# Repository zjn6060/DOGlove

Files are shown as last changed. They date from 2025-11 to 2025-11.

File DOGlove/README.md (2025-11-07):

#A new fork from Jianai Zhao

# <a href="https://do-glove.github.io/">DOGlove: Dexterous Manipulation with a Low-Cost Open-Source Haptic Force Feedback Glove</a>

**Robotics: Science and Systems (RSS) 2025**

<a href="https://do-glove.github.io/"><strong>Project Page</strong></a> | 
<a href="https://arxiv.org/pdf/2502.07730"><strong>Paper</strong></a> | 
<a href="https://tea-lab.github.io/DOGlove/"><strong>Documentation</strong></a> | 
<a href="https://www.bilibili.com/video/BV19SLizUEfa/"><strong>30min工作讲解</strong></a>

[Han Zhang](https://doublehan07.github.io/)<sup>1,2</sup>,
[Songbo Hu](https://hsb0508.github.io/)<sup>1</sup>,
[Zhecheng Yuan](https://gemcollector.github.io/)<sup>1,2,3</sup>
[Huazhe Xu](http://hxu.rocks/)<sup>1,2,3</sup>

<sup>1</sup>Tsinghua University,
<sup>2</sup>Shanghai Qi Zhi Institute,
<sup>3</sup>Shanghai AI Lab

<div align="center">
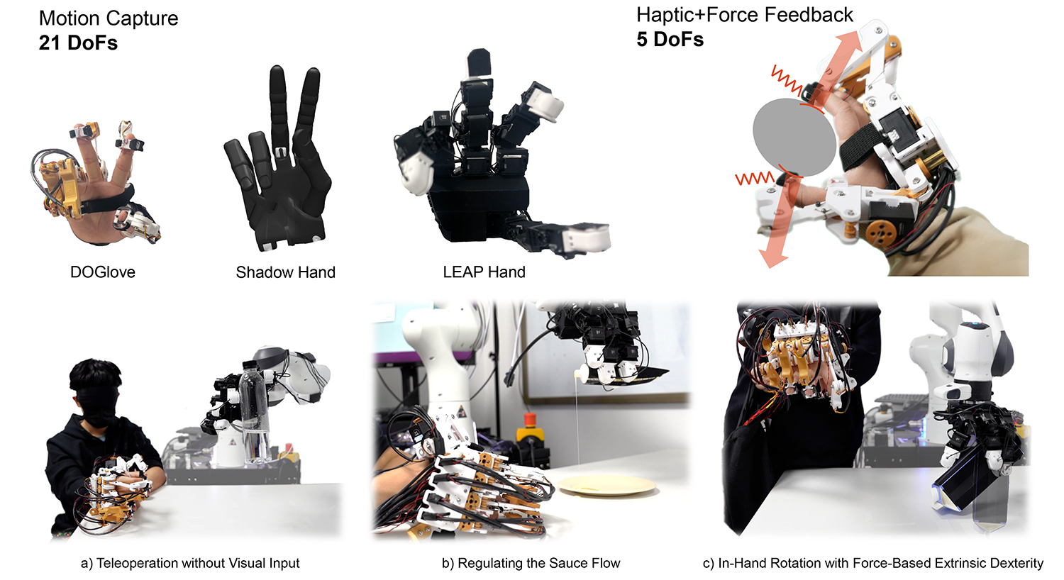
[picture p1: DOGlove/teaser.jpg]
teaser
  
</div>

## 🐣 Updates
* **2025/04/28** — Initial commit.
* **2025/05/11** — Added embedded firmware repository.
* **2025/06/01** — Added MakerWorld link, PCBA files, and Onshape model link.
* **2025/06/22** — Update the tutorial. Add the Python scripts.

## 🛠️ Environment Setup
**Tested on:** Ubuntu 20.04 LTS

### 1. Create Conda Environment
```bash
conda create -n DOGlove python=3.9.19
```

### 2. Install MuJoCo
```bash
conda install -c conda-forge mujoco
```

### 3. Install Required Python Packages
```bash
pip install -r requirements.txt
```

### 4. Install Dynamixel Wizard
Follow the [official installation guide](https://emanual.robotis.com/docs/en/software/dynamixel/dynamixel_wizard2/#install-linux):

1. Download the installer:
   [Linux Download](http://www.robotis.com/service/download.php?no=1671)
2. Grant permission:
   ```bash
   sudo chmod 775 DynamixelWizard2Setup_x64
   ```
3. Run the installer:
   ```bash
   ./DynamixelWizard2Setup_x64
   ```
4. Follow the prompts to complete installation.
5. Add your user to the `dialout` group to access the USB port:
   ```bash
   sudo usermod -aG dialout <your_account_id>
   # You can find your ID using:
   whoami
   ```
6. Reboot to apply the changes:
   ```bash
   sudo reboot
   ```

## 🧪 Run Test Scripts
```bash
conda activate DOGlove
python servo.py
python glove_mcu.py
python DOGlove_FK.py
```

## 🏷️ License
This repository is released under the MIT license. See [LICENSE](LICENSE) for more details.

## 👍 Acknowledgement
- Our wrist tracking code is adapted from [HTC Vive Tracker Python API](https://github.com/tianshengs/SteamVR_Tracking).
- Our Franka control code is adapted from [UMI](https://github.com/real-stanford/universal_manipulation_interface) and [Data Scaling Laws](https://github.com/Fanqi-Lin/Data-Scaling-Laws).
- Our 3D diffusion policy implementation is adapted from [3D Diffusion Policy](https://github.com/YanjieZe/3D-Diffusion-Policy) and [DemoGen](https://github.com/TEA-Lab/DemoGen).
- The teleoperation baseline (AnyTeleop) is implemented from [Dex Retargeting](https://github.com/dexsuite/dex-retargeting).

Contact [Han Zhang](https://doublehan07.github.io/) if you have any questions or suggestions.

## 📝 Citation
If you find our work useful, please consider citing:
```console
@article{zhang2025doglove,
  title={DOGlove: Dexterous Manipulation with a Low-Cost Open-Source Haptic Force Feedback Glove},
  author={Zhang, Han and Hu, Songbo and Yuan, Zhecheng and Xu, Huazhe},
  journal={arXiv preprint arXiv:2502.07730},
  year={2025}
}
```

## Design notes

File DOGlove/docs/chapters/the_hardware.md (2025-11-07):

# Hardware

DOGlove’s hardware consists of two main components: the electronics for sensing and control, and the mechanical structure for physical interaction.

```{toctree}
:hidden:
:maxdepth: 1

../hardware/01_circuit.rst
../hardware/02_mechanical.md
```

## Circuit Design

Learn how we designed the electronics for DOGlove, including the schematic, PCB layout, and how to import or preview the project:

* [Circuit Design](../hardware/01_circuit.rst)

## Mechanical Design

Explore the mechanical structure of DOGlove through a full Onshape model, which can be exported in various formats:

* [Mechanical Design](../hardware/02_mechanical.md)

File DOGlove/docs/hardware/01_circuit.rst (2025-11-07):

.. _circuit_design:

Circuit Design
==============

The Schematics
--------------

.. raw:: html

   <iframe src="../_static/hardware/SCH_DOGlove_MainCircuit.pdf" width="100%" height="600px"></iframe>

Import the Project File
------------------------

We use lceda (EasyEDA) to design the schematic and PCB layout. To preview the source project, you have two options:

Option 1: Import the `.epro` File
^^^^^^^^^^^^^^^^^^^^^^^^^^^^^^^^^

- **For users in China**: Use the `lceda Pro Edition (立创eda专业版) <https://pro.lceda.cn/editor>`__ to import the `.epro` file.
- **For users in other regions**: Use the `EasyEDA Pro Edition <https://pro.easyeda.com/editor>`__ to import the `.epro` file.

Steps to Import:

1. Download the :download:`ProPrj_DOGlove_MainBoard.epro <../_static/hardware/ProPrj_DOGlove_MainBoard.epro>` file.
2. Open EasyEDA Pro and navigate to ``File → Import → EasyEDA (Professional)``.

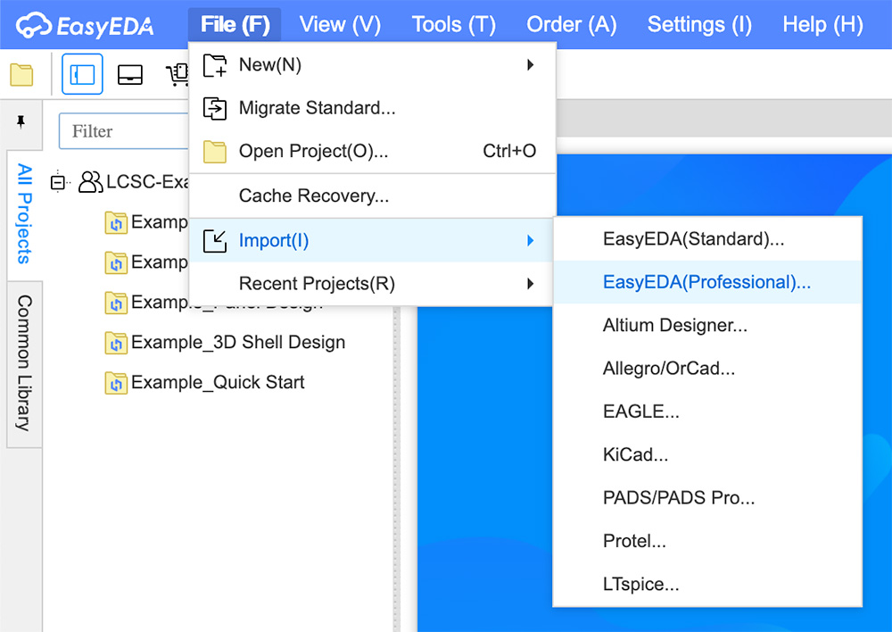
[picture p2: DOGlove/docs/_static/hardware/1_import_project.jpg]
   

3. Upload the `.epro` file, adjust the settings as shown below, then click **Import**:
   
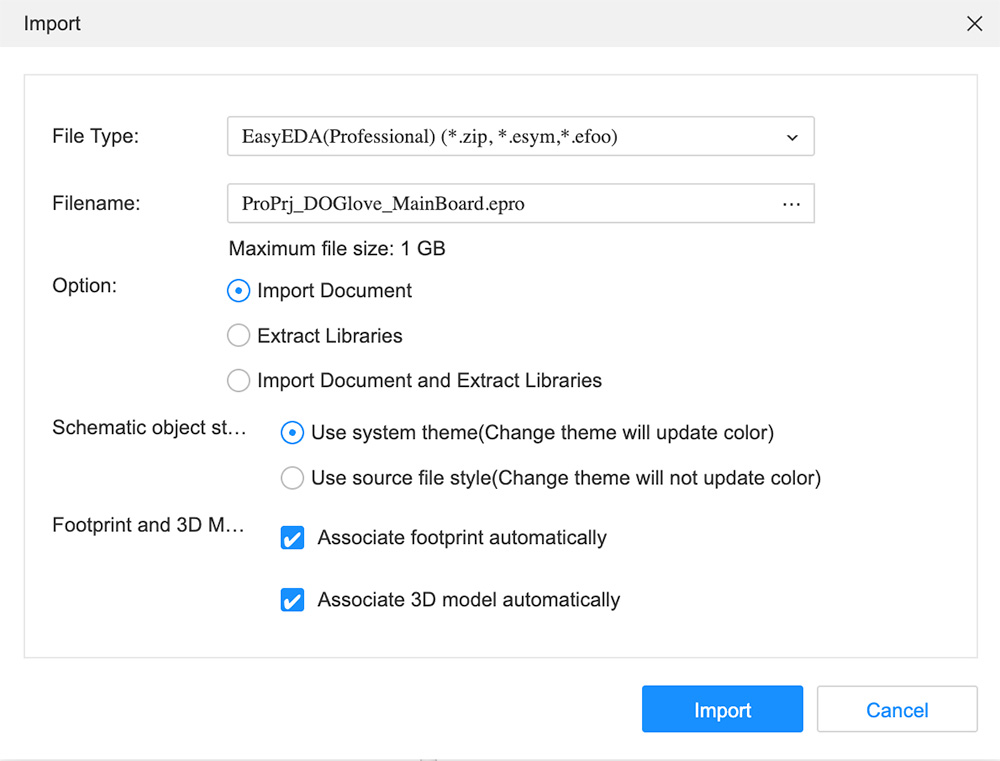
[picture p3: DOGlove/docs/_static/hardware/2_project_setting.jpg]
   

4. Confirm the import settings and click **Save**:

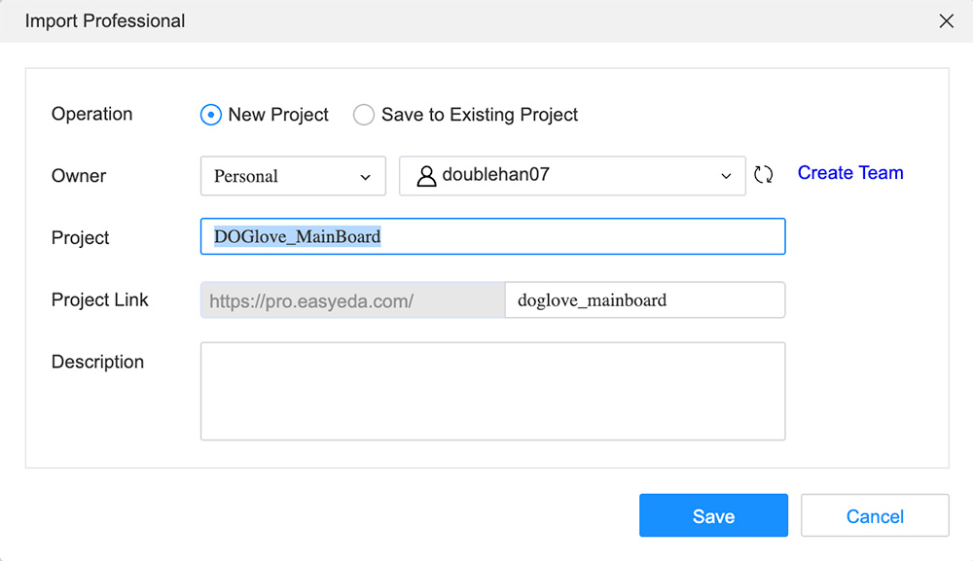
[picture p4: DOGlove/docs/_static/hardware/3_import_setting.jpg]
   

5. You should now see the full schematic and layout preview:

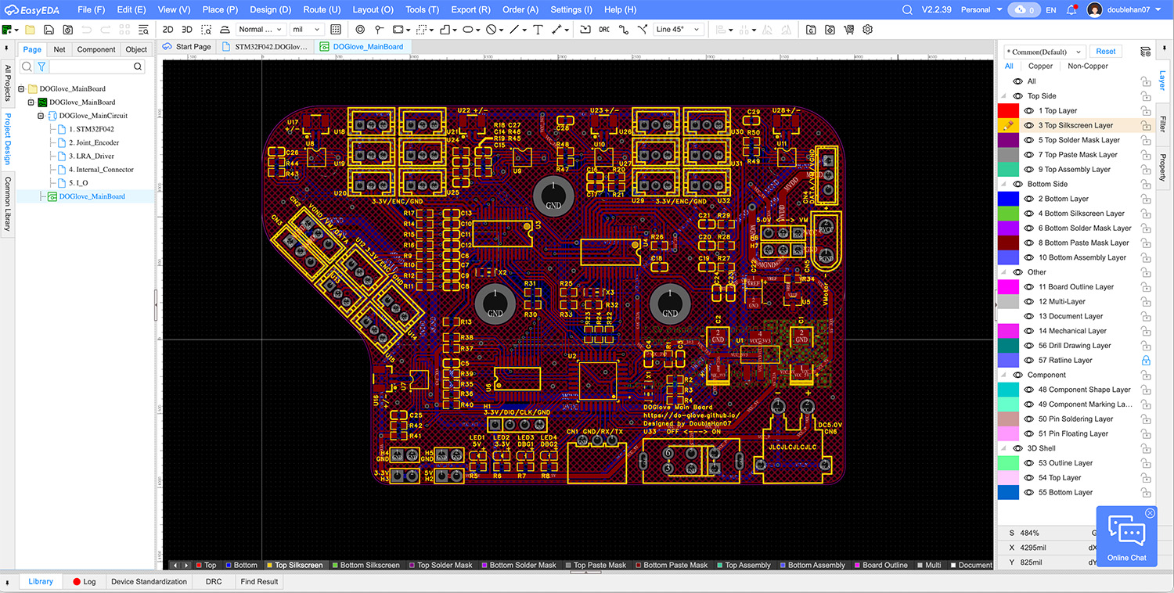
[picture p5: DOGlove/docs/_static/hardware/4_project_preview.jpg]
   

Option 2: View on OSHWHub (Recommended for Users in China)
^^^^^^^^^^^^^^^^^^^^^^^^^^^^^^^^^^^^^^^^^^^^^^^^^^^^^^^^^^^

You can directly view the `DOGlove project on OSHWHub (立创开源硬件平台) <https://oshwhub.com/doublehan/doglove_mainboard>`__, which includes the schematics, PCB layout, and BOM. The platform also supports one-click PCB fabrication.

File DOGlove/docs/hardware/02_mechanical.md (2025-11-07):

# Mechanical Design

You can view the 3D model of DOGlove on Onshape. The model can be exported to SolidWorks, STEP, IGES, STL, and other formats supported by Onshape.

[🧩 Onshape: 3D Model](https://cad.onshape.com/documents/7fa03943c40f265f7147311f)

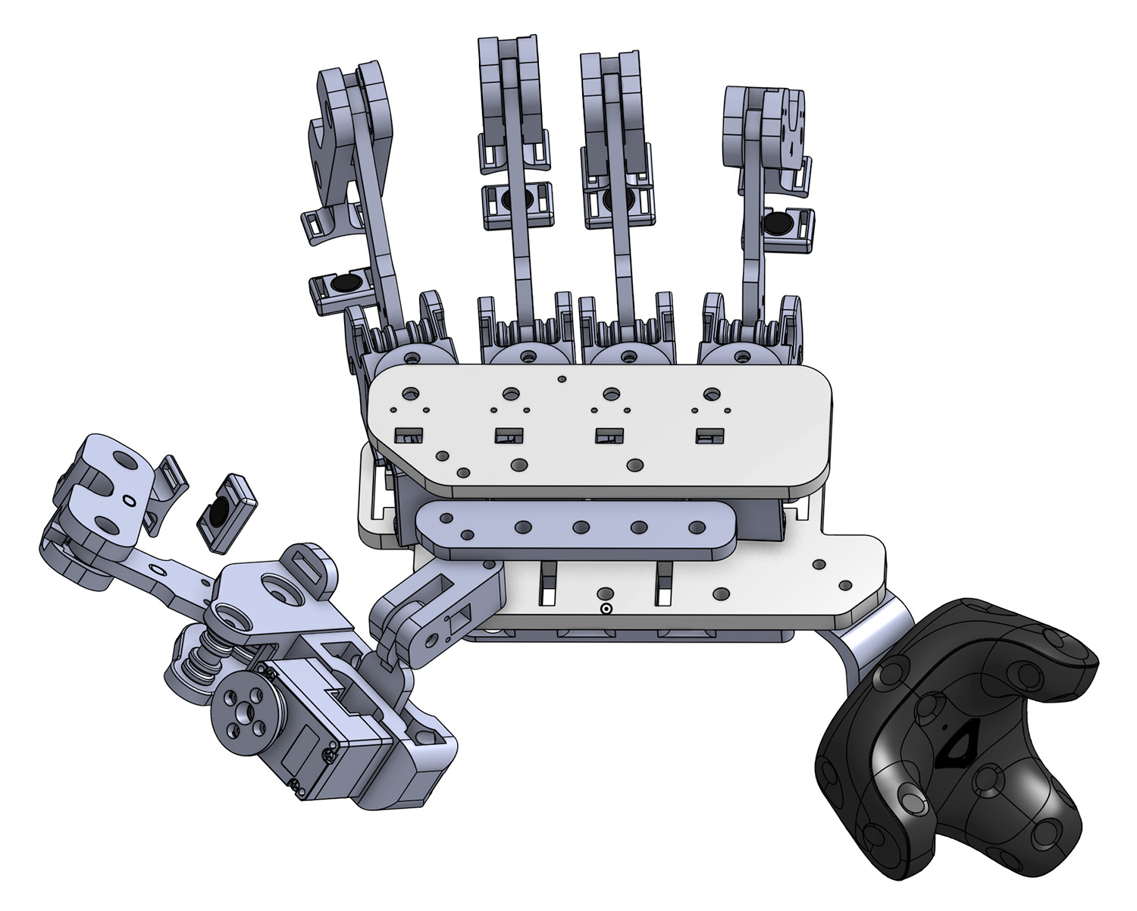
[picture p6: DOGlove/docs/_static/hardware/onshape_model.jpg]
Onshape Model Preview


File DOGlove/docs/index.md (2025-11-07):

# DOGlove

DOGlove is a low-cost, open-source haptic+force feedback glove designed for dexterous manipulation and teleoperation.  

Check out some useful links below to learn more:

[🌐 Website](https://do-glove.github.io/) | 
[📄 Paper](https://arxiv.org/pdf/2502.07730) | 
[🎥 Video](https://www.youtube.com/watch?v=2qO7dbH9zxc) | 
[𝕏 Tweet](https://x.com/DoubleHan07/status/1889815837810499688)

[🧩 Onshape: 3D Model](https://cad.onshape.com/documents/7fa03943c40f265f7147311f)

[🛠️ MakerWorld: Bambu 3mf Files](https://makerworld.com/en/models/1476400-doglove#profileId-1541008)

[📟 Circuit Board: OSHWHub (lceda)](https://oshwhub.com/doublehan/doglove_mainboard)

[⚙️ Firmware: STM32 Source Code](https://github.com/doublehan07/DOGlove_Firmware)

---

## Getting Started

Ready to dive in? We've prepared a [detailed tutorial](chapters/getting_started) to help you build your own DOGlove!

If you're new to DOGlove, the easiest way is to follow the step-by-step tutorial☝️.  
For experienced developers, we also highlight the key steps below👇:

- **Flash the embedded firmware**: Check out the [firmware](quick_start/03_flash_firmware) script.
- **Bring it to life**: Quick link to [make it move](quick_start/05_make_it_move).

## Customizing

Want to customize your DOGlove, explore the key design ideas, or contribute to the project?  
Check out the following sections for more details!

* [Hardware](chapters/the_hardware): Circuit design details and 3D printable models.
* [Firmware](chapters/the_firmware): Embedded firmware that runs on DOGlove.
* [Software](chapters/the_software): Python API and interface to control DOGlove.

## Troubleshooting

<!-- If you encounter any issues or have suggestions for improvements, feel free to [open a GitHub issue]()!   -->
If you encounter any issues or have suggestions for improvements, feel free to open a GitHub issue.   
We'd love to hear from you.

```{toctree}
:maxdepth: 1
:hidden:

chapters/getting_started
chapters/the_hardware
chapters/the_firmware
chapters/the_software

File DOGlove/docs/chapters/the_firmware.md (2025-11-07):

# Firmware

The source code of the firmware is listed [here](https://github.com/doublehan07/DOGlove_Firmware).

## Use the Firmware

You can download the precompiled firmware from the following link and flash it to the STM32:
[DOGlove.hex](https://github.com/doublehan07/DOGlove_Firmware/releases/download/v1.0/DOGlove.hex)

## Build from Source Code

To build the firmware from source:

```bash
git clone https://github.com/doublehan07/DOGlove_Firmware.git
cd DOGlove_Firmware
make
```

> 💡 Note: You may need to install [arm-none-eabi-gcc](https://developer.arm.com/downloads/-/gnu-rm) to compile the firmware.

## Notes for Advanced Developers

To modify the firmware or view pin configurations, open the [DOGlove.ioc](https://github.com/doublehan07/DOGlove_Firmware/blob/main/DOGlove.ioc) file using [STM32CubeMX](https://www.st.com/en/development-tools/stm32cubemx.html).

### Pin Allocation

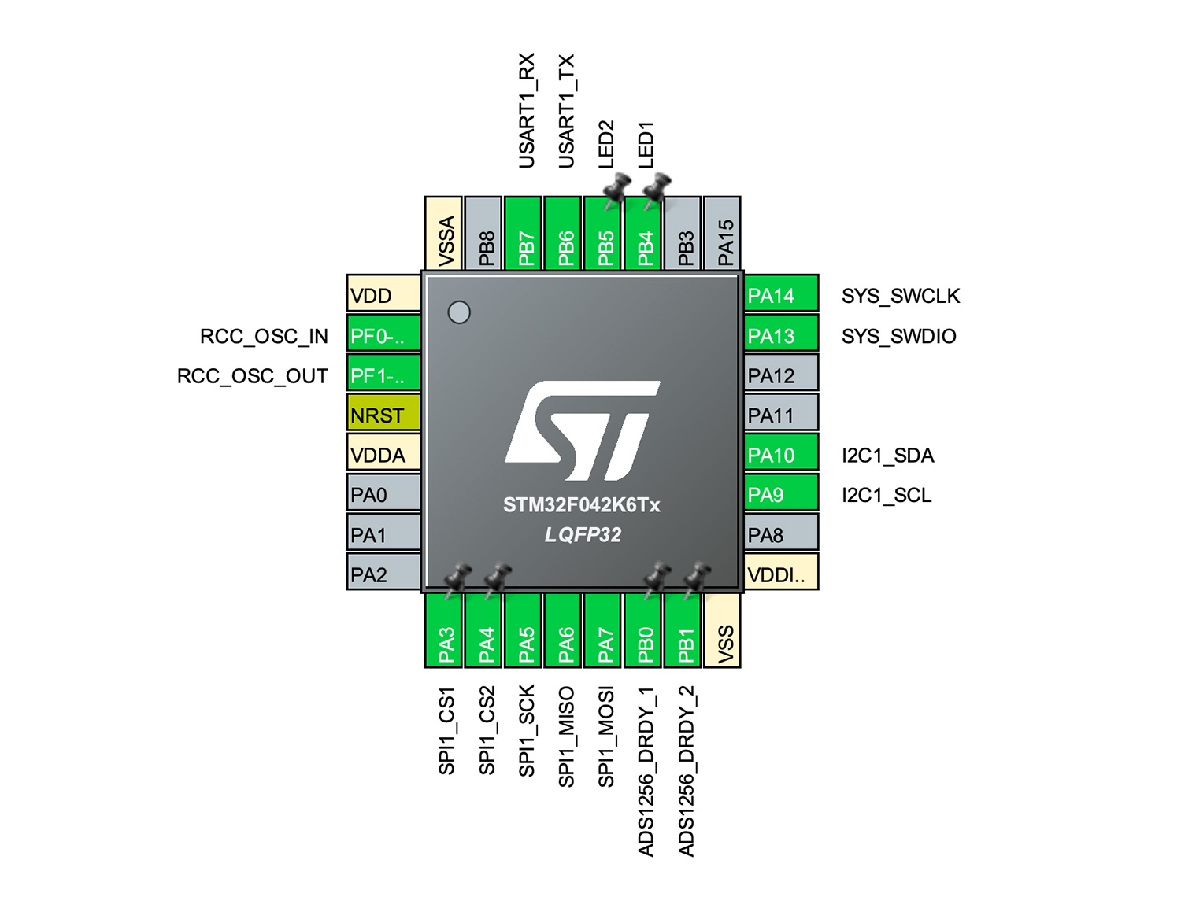
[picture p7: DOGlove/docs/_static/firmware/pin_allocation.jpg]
Pin Allocation


### Clock Tree Configuration

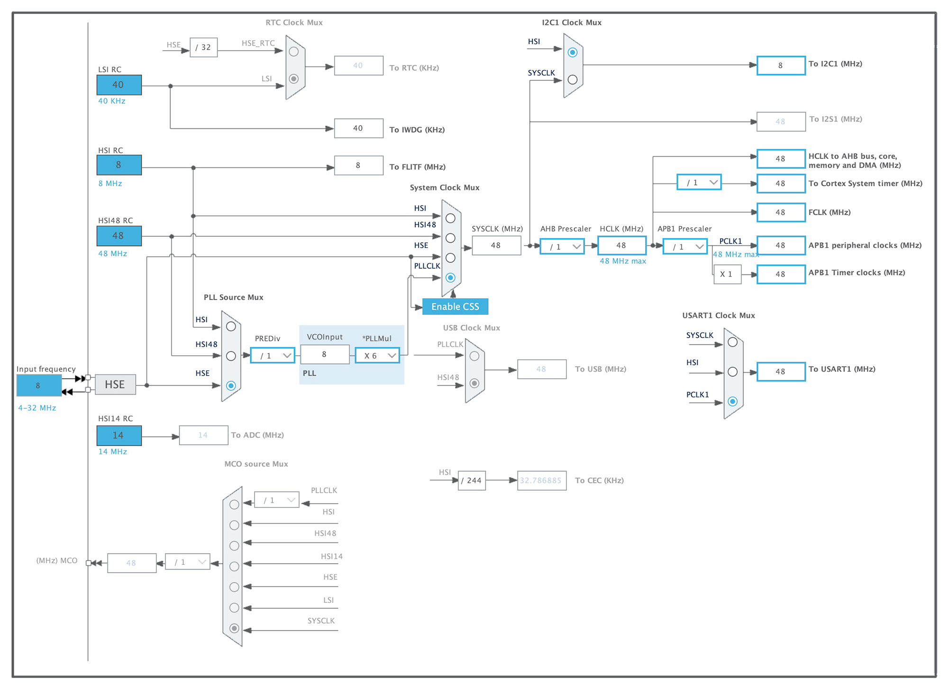
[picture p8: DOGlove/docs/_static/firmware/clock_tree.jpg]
Clock Tree


### Source Code Structure

* [/Core](https://github.com/doublehan07/DOGlove_Firmware/tree/main/Core): *(Auto-generated by STM32CubeMX, except for `main.c` and `stm32f0xx_it.c`)*

  * [main.c](https://github.com/doublehan07/DOGlove_Firmware/blob/main/Core/Src/main.c): System initialization, LRA control, and encoder data packaging.
  * [stm32f0xx\_it.c](https://github.com/doublehan07/DOGlove_Firmware/blob/main/Core/Src/stm32f0xx_it.c): SysTick handler used for system-level scheduling.

* [/Drivers](https://github.com/doublehan07/DOGlove_Firmware/tree/main/Drivers): STM32 HAL drivers *(auto-generated)*

* [/Users](https://github.com/doublehan07/DOGlove_Firmware/tree/main/Users): Custom drivers and application code.

  * [ads1256.c](https://github.com/doublehan07/DOGlove_Firmware/blob/main/Users/ads1256.c): ADC driver for the ADS1256 chip.
  * [drv2605l.c](https://github.com/doublehan07/DOGlove_Firmware/blob/main/Users/drv2605l.c): Haptic driver for the DRV2605L chip.
  * [tca9548a.c](https://github.com/doublehan07/DOGlove_Firmware/blob/main/Users/tca9548a.c): I2C multiplexer driver for the TCA9548A chip.
  * [fsr.c](https://github.com/doublehan07/DOGlove_Firmware/blob/main/Users/fsr.c): Reads power supply voltage via STM32's internal ADC.
  * [delay.c](https://github.com/doublehan07/DOGlove_Firmware/blob/main/Users/delay.c): Implements precise millisecond-level delay.
  * [lra\_control.c](https://github.com/doublehan07/DOGlove_Firmware/blob/main/Users/lra_control.c): LRA control logic and UART RX event callback.

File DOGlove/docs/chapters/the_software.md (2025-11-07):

# Software

This section outlines the key components of the software stack for DOGlove, including communication protocols, servo control, feedback mechanisms, and calibration.

## Communication Between PC and Main Board

- **UART Package** – Used for low-level serial communication.  
- **Vibration Package** – Responsible for encoding and transmitting vibration feedback.  
- **UDP** – Used for real-time data streaming between the glove and host computer.

## Servo Data Path

- **UDP** – Servo position commands and sensor data are transmitted over UDP for low-latency control.

## Haptic + Force Feedback

- **Force Sensor Readings** – Captures contact forces at the robot fingertips.
- **Force Feedback Activation Threshold** –  
  When the measured force exceeds a preset threshold, force feedback is enabled by turning on `servo.torque`.

  - To adjust the *stiffness* of the force feedback, modify the `Kp` gain parameter.

- **Vibration Activation Threshold** –  
  When a separate threshold is crossed, the MCU sends vibration commands to the glove.

  - You can adjust the **vibration pattern** and **duration** using the TI vibration library.

## Forward and Inverse Kinematics (FK & IK)

- Add the **site name** in the corresponding `.xml` file to support FK/IK calculations for the pinky finger.

## Calibration: Scale and Shift

To ensure realistic hand motion mapping, we apply scale and shift adjustments:

- **Finger Length Discrepancy → Scale Factor**  
  Scale the glove’s finger motion to match the relative lengths of the robotic hand.

- **Finger Distance Discrepancy → Shift Offset**  
  Adjust for base position differences between fingers to ensure accurate positioning.

The goal is simple: when the real thumb and index finger touch, the robot’s thumb and index should touch as well.

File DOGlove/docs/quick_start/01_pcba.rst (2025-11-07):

.. _tutorials_en:

=================
PCB Assembly
=================

- `Step-by-step Tutorial (English) <#tutorials_en>`_

Step-by-Step Guide to Ordering PCBA
====================================

This tutorial walks you through how to order the DOGlove main board through `JLCPCB <https://cart.jlcpcb.com/quote>`_.

.. note::
   You're free to choose any PCBA manufacturer you prefer. In general, you'll need to submit a **Gerber file** (for PCB fabrication) and **Pick & Place + BOM files** (for SMT assembly).

1. File Preparation
-------------------

- :download:`Download Gerber file <../_static/quick_start/pcba/Gerber_DOGlove_MainBoard.zip>`
- :download:`Download Pick & Place file <../_static/quick_start/pcba/PickAndPlace_DOGlove_MainBoard.xlsx>`
- :download:`Download BOM file <../_static/quick_start/pcba/BOM_DOGlove_MainBoard_DOGlove_MainBoard.xlsx>`

2. Order the PCB
------------------

**Step 1:** Upload the Gerber file you just downloaded.

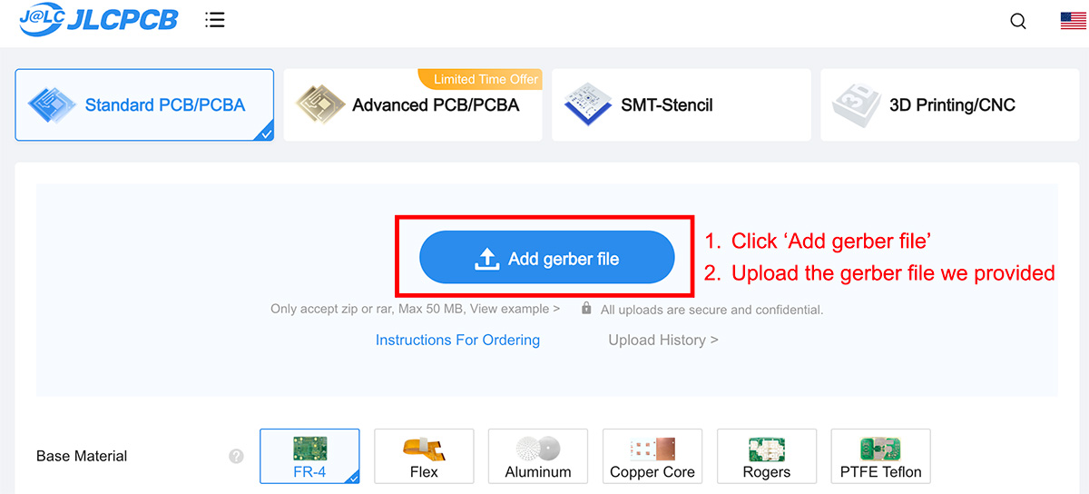
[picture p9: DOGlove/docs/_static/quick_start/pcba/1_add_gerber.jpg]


**Step 2:** Follow the image tutorial below to select the appropriate manufacturing parameters.

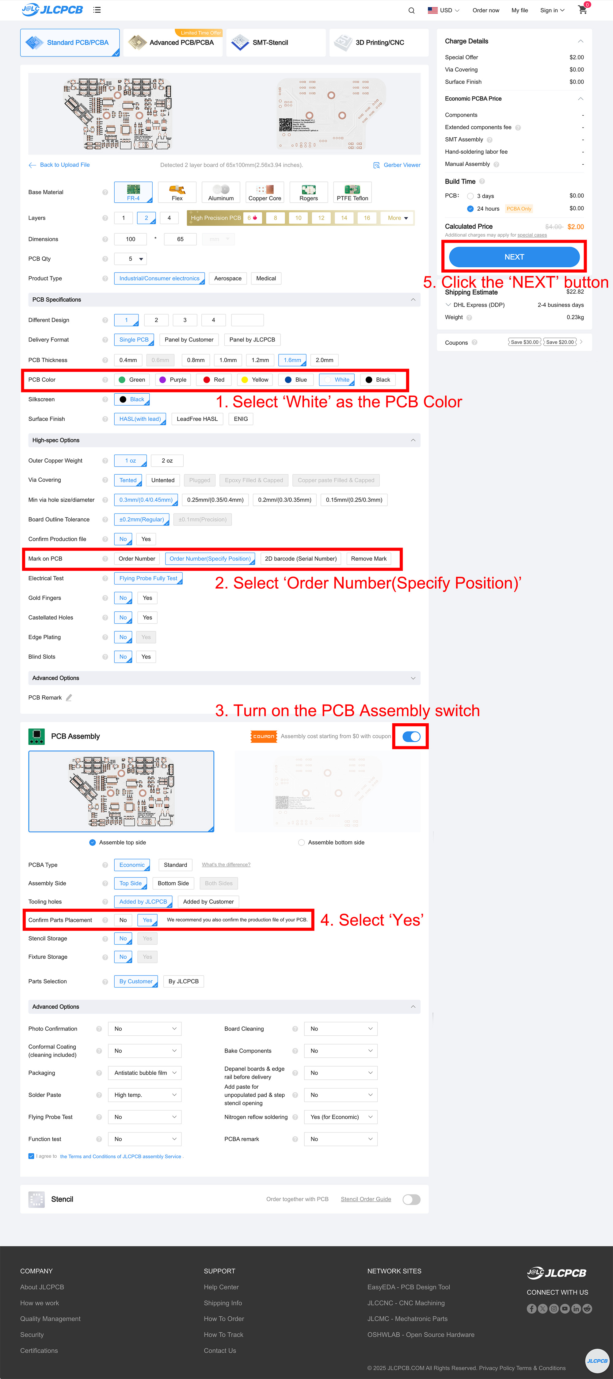
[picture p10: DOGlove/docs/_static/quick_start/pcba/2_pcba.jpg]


**Step 3:** On the next page, open the ``Bill of Materials`` section and upload both the **BOM** and **Pick & Place** files.

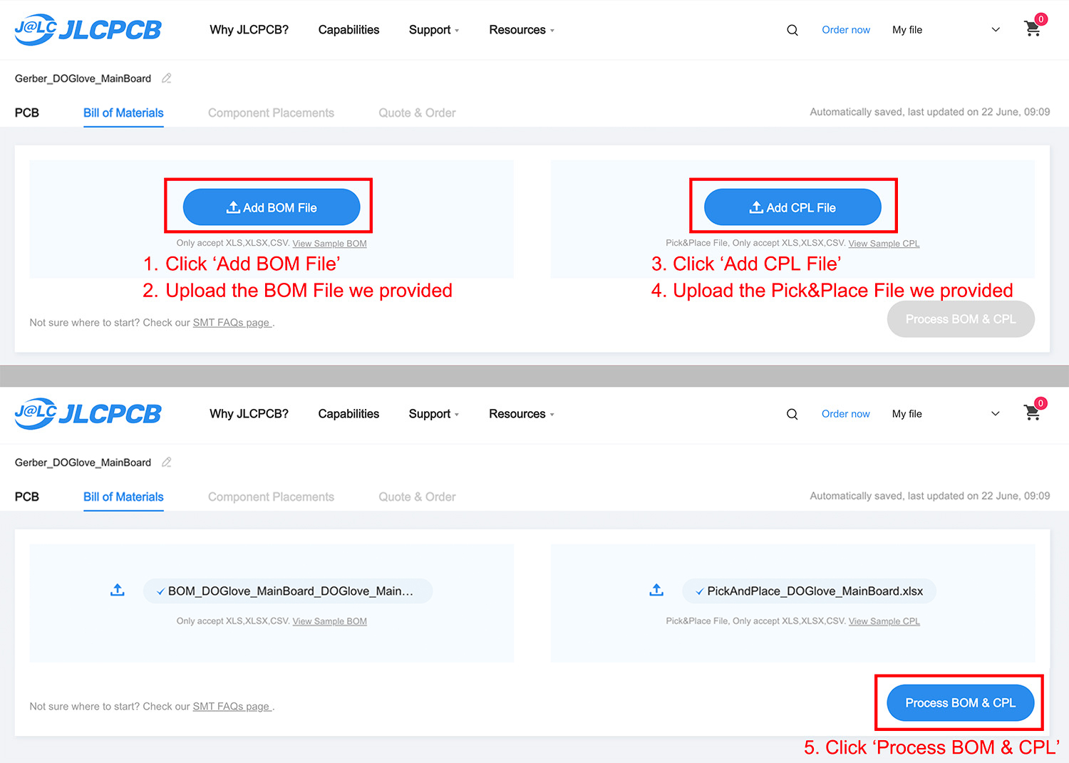
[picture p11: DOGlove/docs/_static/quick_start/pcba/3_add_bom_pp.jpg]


**Step 4:** Once processed, a parts confirmation list will be shown. If all parts are in stock, click **NEXT** to proceed.

.. tip::
   If some parts are unavailable, manually select substitutes using the suggestions provided. 

   Need help? Open a GitHub issue or contact Han directly.

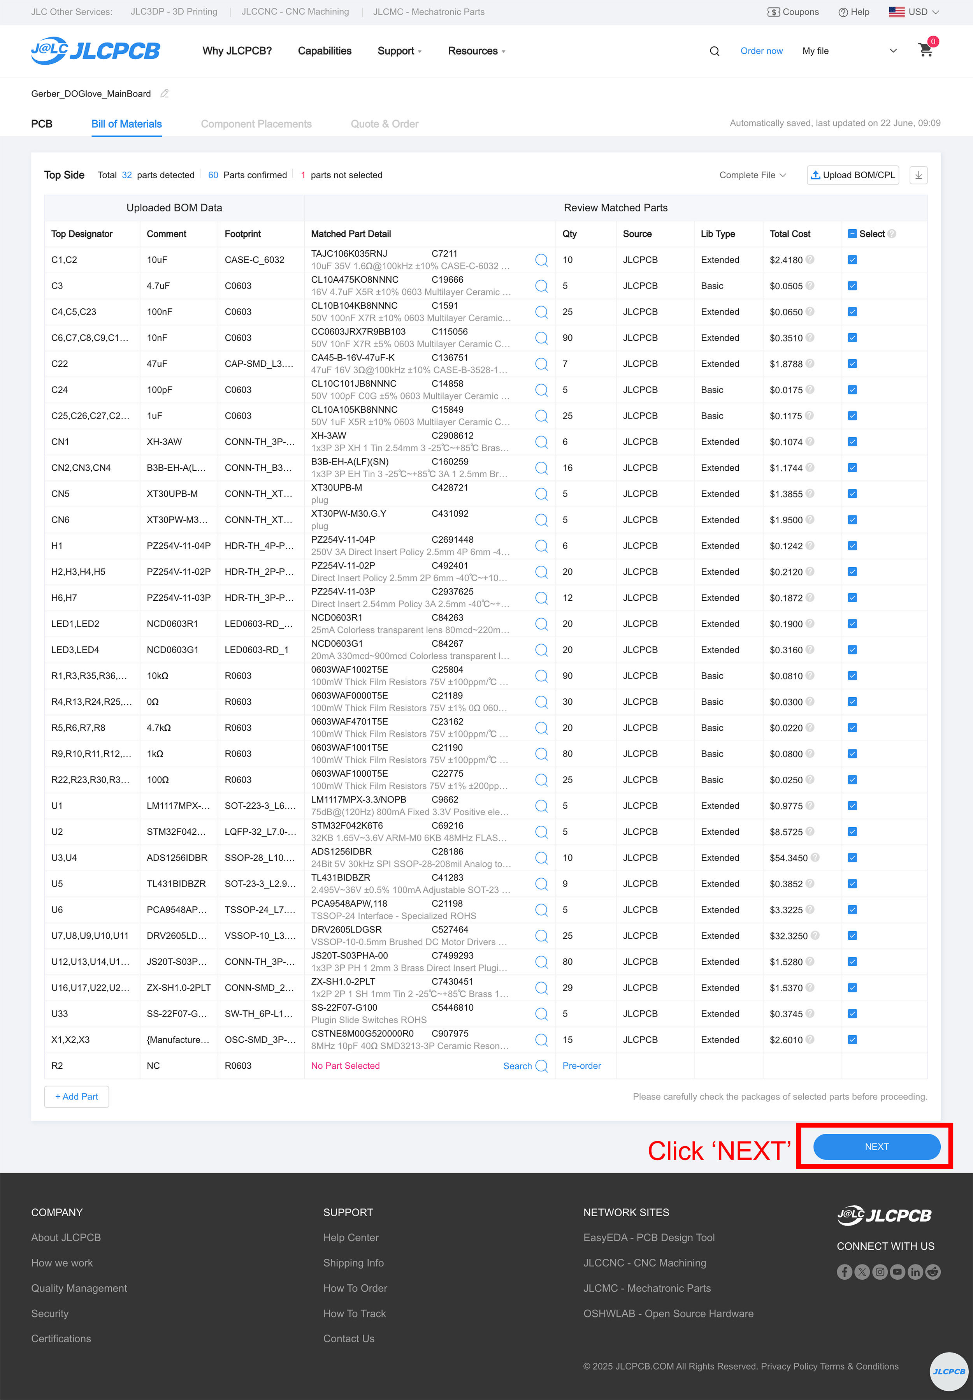
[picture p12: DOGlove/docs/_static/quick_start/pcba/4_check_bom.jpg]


**Step 5:** You might see a warning like *"Project has unselected parts."* This is normal, as some NC (Not Connected) parts are not meant to be assembled. Just click **Do not place** to continue.

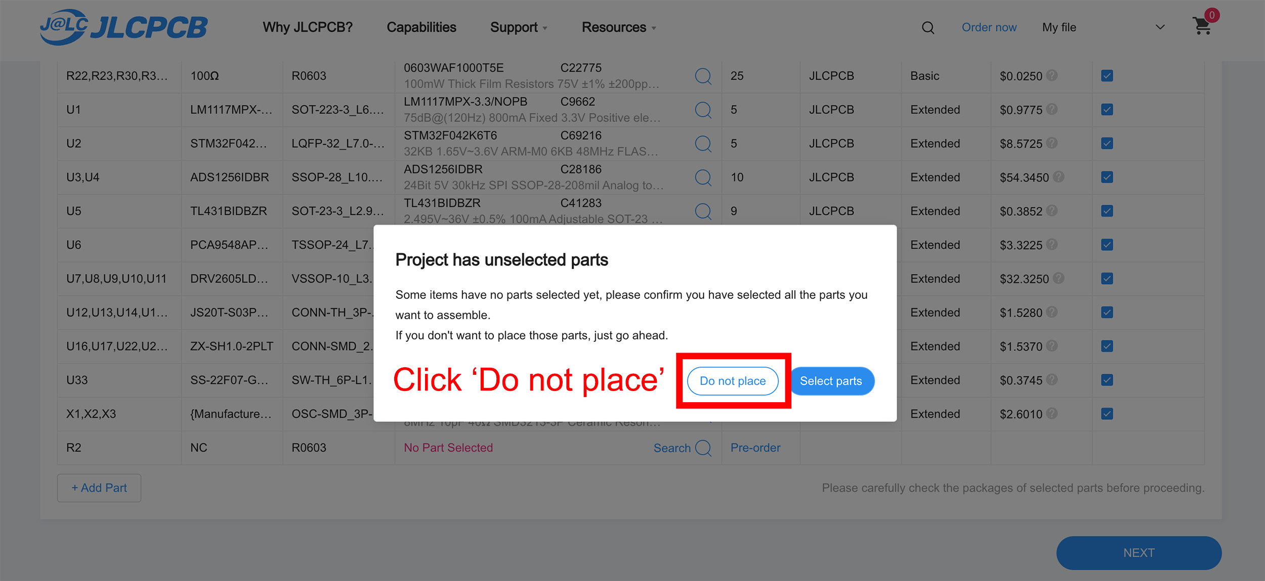
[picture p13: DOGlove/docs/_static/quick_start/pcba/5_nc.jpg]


**Final Step:** 🎉 You’re almost there! You can now preview a 3D model of your assembled board. If everything looks good and matches the preview images, click **NEXT** to place your order!

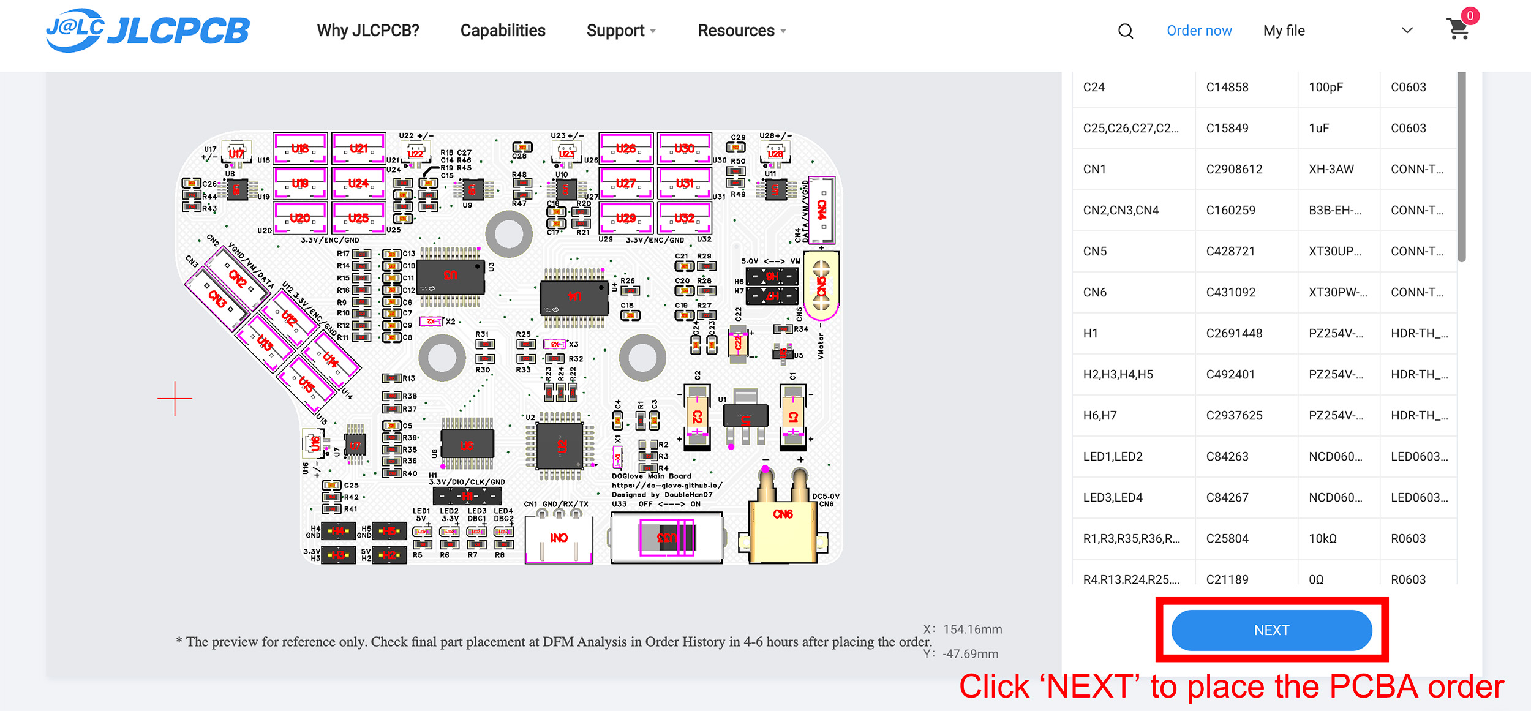
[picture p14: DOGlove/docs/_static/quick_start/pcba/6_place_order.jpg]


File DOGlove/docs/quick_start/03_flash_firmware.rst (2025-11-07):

.. _flash-firmware:

Flash the Firmware
==================

First, follow the image below to correctly connect the main board to the ST-Link V2.

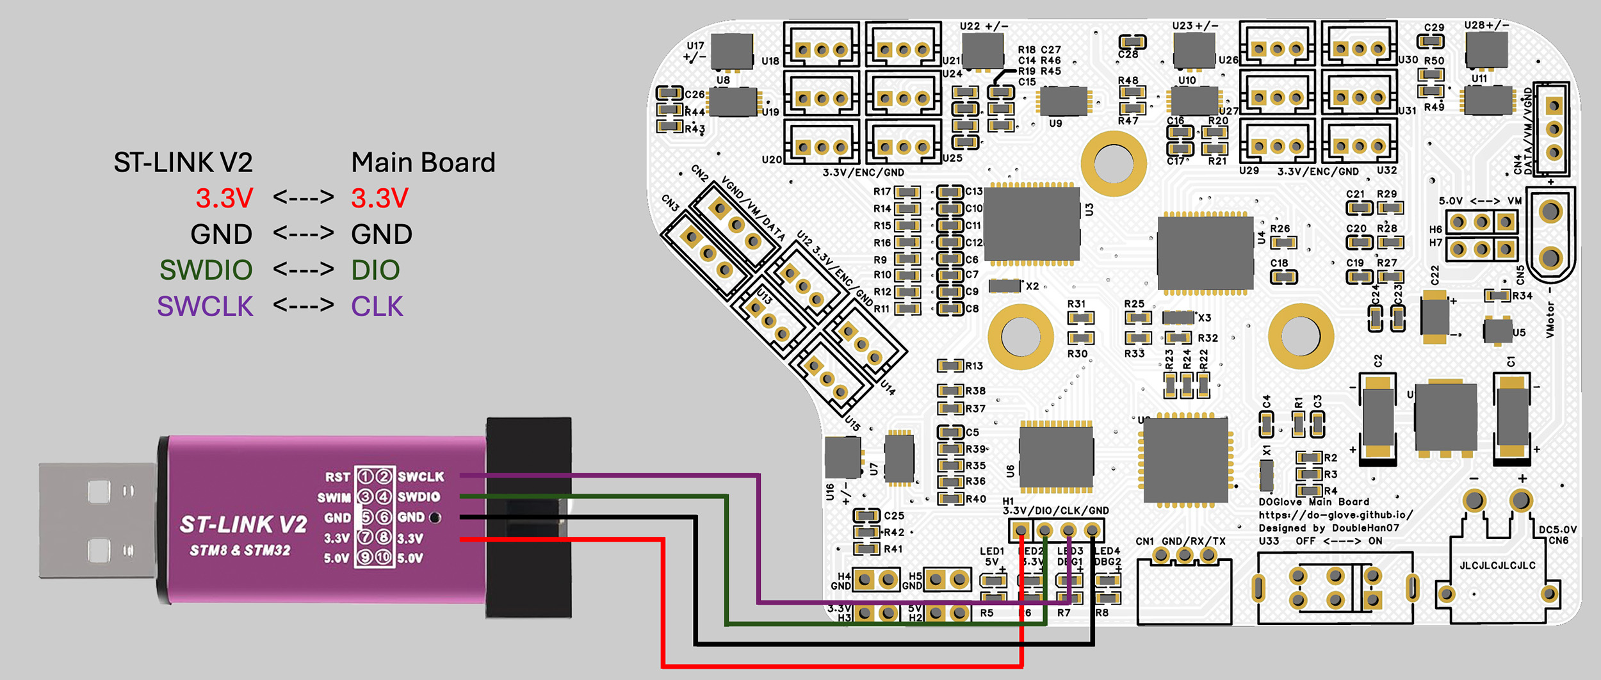
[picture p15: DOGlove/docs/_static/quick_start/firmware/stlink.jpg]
Connect main board to ST-Link V2


Next, download the latest firmware:

- :download:`DOGlove firmware <https://github.com/doublehan07/DOGlove_Firmware/releases/download/v1.0/DOGlove.hex>`

Then you need a tool to flash the firmware into the STM32 MCU (Microcontroller).

For Ubuntu, we suggest `openocd <https://openocd.org/pages/getting-openocd.html>`_.

.. note::

   Our whole system is verified under Ubuntu 20.04. 
   
   For macOS, you can also use `openocd` by running ``brew install open-ocd``. 
   
   For Windows, consider using the `STM32Programmer <https://www.st.com/en/development-tools/stm32cubeprog.html>`_.

To install openocd, simply type this command:

.. code-block:: bash

   sudo apt-get install openocd

Then change directory to the firmware location:

.. code-block:: bash

   cd <YOUR_FIRMWARE_LOCATION>
   openocd -f interface/stlink-v2.cfg -f target/stm32f0x.cfg -c "program DOGlove.hex verify reset exit"

If everything goes well, you might see the following message:

.. code-block:: text

   flash verify OK

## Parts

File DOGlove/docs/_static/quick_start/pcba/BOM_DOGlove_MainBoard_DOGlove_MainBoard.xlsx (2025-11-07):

No. | Quantity | Comment | Designator | Footprint | Value | Manufacturer Part | Manufacturer | Supplier Part | Supplier
1 | 2 | 10uF | C1,C2 | CASE-C_6032 | 10uF | TAJC106K035RNJ | Kyocera AVX | C7211 | LCSC
2 | 1 | 4.7uF | C3 | C0603 | 4.7uF | CL10A475KO8NNNC | SAMSUNG(三星) | C19666 | LCSC
3 | 3 | 100nF | C4,C5,C23 | C0603 | 100nF | CL10B104KB8NNNC | SAMSUNG(三星) | C1591 | LCSC
4 | 16 | 10nF | C6,C7,C8,C9,C10,C11,C12,C13,C14,C15,C16,C17,C18,C19,C20,C21 | C0603 | 10nF | CC0603JRX7R9BB103 | YAGEO(国巨) | C115056 | LCSC
5 | 1 | 47uF | C22 | CAP-SMD_L3.5-W2.8-R-RD | 47uF | CA45-B-16V-47uF-K | CEC(振华新云) | C136751 | LCSC
6 | 1 | 100pF | C24 | C0603 | 100pF | CL10C101JB8NNNC | SAMSUNG(三星) | C14858 | LCSC
7 | 5 | 1uF | C25,C26,C27,C28,C29 | C0603 | 1uF | CL10A105KB8NNNC | SAMSUNG(三星) | C15849 | LCSC
8 | 1 | XH-3AW | CN1 | CONN-TH_3P-P2.54_HCTL_XH-3AW |  | XH-3AW | HCTL(华灿天禄) | C2908612 | LCSC
9 | 3 | B3B-EH-A(LF)(SN) | CN2,CN3,CN4 | CONN-TH_B3B-EH-A-LF-SN |  | B3B-EH-A(LF)(SN) | JST | C160259 | LCSC
10 | 1 | XT30UPB-M | CN5 | CONN-TH_XT30UPB-M |  | XT30UPB-M | AMASS(艾迈斯) | C428721 | LCSC
11 | 1 | XT30PW-M30.G.Y | CN6 | CONN-TH_XT30PW-M |  | XT30PW-M30.G.Y | AMASS(艾迈斯) | C431092 | LCSC
12 | 1 | PZ254V-11-04P | H1 | HDR-TH_4P-P2.54-V-M |  | PZ254V-11-04P | XFCN(兴飞) | C2691448 | LCSC
13 | 4 | PZ254V-11-02P | H2,H3,H4,H5 | HDR-TH_2P-P2.54-V-M |  | PZ254V-11-02P | XFCN(兴飞) | C492401 | LCSC
14 | 2 | PZ254V-11-03P | H6,H7 | HDR-TH_3P-P2.54-V-M |  | PZ254V-11-03P | XFCN(兴飞) | C2937625 | LCSC
15 | 2 | NCD0603R1 | LED1,LED2 | LED0603-RD_RED |  | NCD0603R1 | 国星光电 | C84263 | LCSC
16 | 2 | NCD0603G1 | LED3,LED4 | LED0603-RD_1 |  | NCD0603G1 | 国星光电 | C84267 | LCSC
17 | 18 | 10kΩ | R1,R3,R35,R36,R37,R38,R39,R40,R41,R42,R43,R44,R45,R46,R47,R48,R49,R50 | R0603 | 10kΩ | 0603WAF1002T5E | UNI-ROYAL(厚声) | C25804 | LCSC
18 | 1 | NC | R2 | R0603 | NC | 0603WAF0000T5E | UNI-ROYAL(厚声) |  | LCSC
19 | 6 | 0Ω | R4,R13,R24,R25,R31,R33 | R0603 | 0Ω | 0603WAF0000T5E | UNI-ROYAL(厚声) | C21189 | LCSC
20 | 4 | 4.7kΩ | R5,R6,R7,R8 | R0603 | 4.7kΩ | 0603WAF4701T5E | UNI-ROYAL(厚声) | C23162 | LCSC
21 | 16 | 1kΩ | R9,R10,R11,R12,R14,R15,R16,R17,R18,R19,R20,R21,R26,R27,R28,R29 | R0603 | 1kΩ | 0603WAF1001T5E | UNI-ROYAL(厚声) | C21190 | LCSC
22 | 5 | 100Ω | R22,R23,R30,R32,R34 | R0603 | 100Ω | 0603WAF1000T5E | UNI-ROYAL(厚声) | C22775 | LCSC
23 | 1 | LM1117MPX-3.3/NOPB | U1 | SOT-223-3_L6.5-W3.4-P2.30-LS7.0-BR |  | LM1117MPX-3.3/NOPB | TI(德州仪器) | C9662 | LCSC
24 | 1 | STM32F042K6T6 | U2 | LQFP-32_L7.0-W7.0-P0.80-LS9.0-BL |  | STM32F042K6T6 | ST(意法半导体) | C69216 | LCSC
25 | 2 | ADS1256IDBR | U3,U4 | SSOP-28_L10.2-W5.3-P0.65-LS7.8-BL |  | ADS1256IDBR | TI(德州仪器) | C28186 | LCSC
26 | 1 | TL431BIDBZR | U5 | SOT-23-3_L2.9-W1.3-P1.90-LS2.4-BR |  | TL431BIDBZR | TI(德州仪器) | C41283 | LCSC
27 | 1 | PCA9548APW,118 | U6 | TSSOP-24_L7.8-W4.4-P0.65-LS6.4-BL |  | PCA9548APW,118 | NXP(恩智浦) | C21198 | LCSC
28 | 5 | DRV2605LDGSR | U7,U8,U9,U10,U11 | VSSOP-10_L3.0-W3.0-P0.50-LS4.9-BL |  | DRV2605LDGSR | TI(德州仪器) | C527464 | LCSC
29 | 16 | JS20T-S03PHA-00 | U12,U13,U14,U15,U18,U19,U20,U21,U24,U25,U26,U27,U29,U30,U31,U32 | CONN-TH_3P-P2.00_BX-PH2.0-3PZZ |  | JS20T-S03PHA-00 | JS(钜硕电子) | C7499293 | LCSC
30 | 5 | ZX-SH1.0-2PLT | U16,U17,U22,U23,U28 | CONN-SMD_2P-P1.00_MEGASTAR_ZX-SH1.0-2PLT |  | ZX-SH1.0-2PLT | Megastar(兆星) | C7430451 | LCSC
31 | 1 | SS-22F07-G100 | U33 | SW-TH_6P-L16.5-W7.5-P4.0-LS2.6-TL |  | SS-22F07-G100 | G-Switch(品赞) | C5446810 | LCSC
32 | 3 | {ManufacturerPart!} | X1,X2,X3 | OSC-SMD_3P-L3.2-W1.3-P1.20 |  | CSTNE8M00G520000R0 | muRata(村田) | C907975 | LCSC

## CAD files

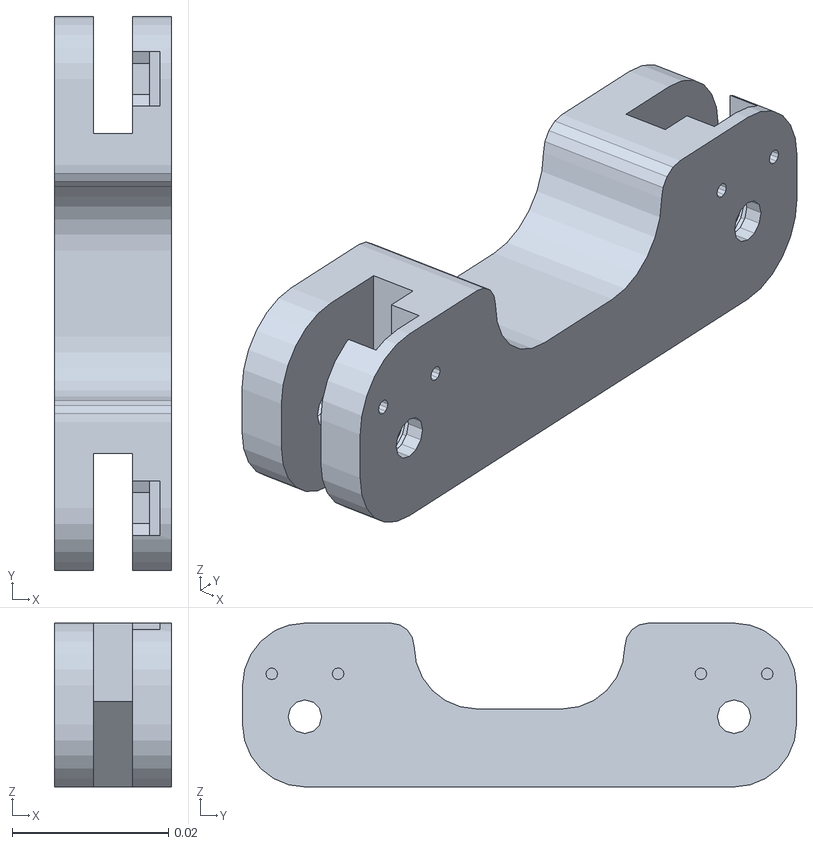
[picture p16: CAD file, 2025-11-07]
DOGlove/DOGlove_meshes/pinky_bend_2.STL
0.015 x 0.071 x 0.021

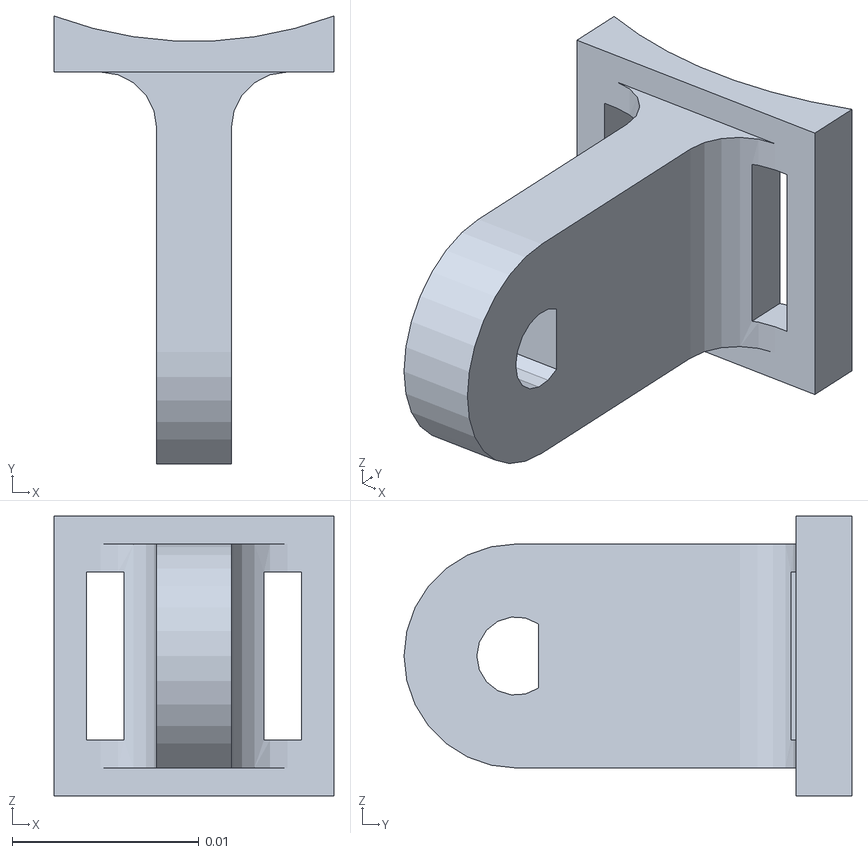
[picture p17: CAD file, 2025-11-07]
DOGlove/DOGlove_meshes/index_bend_1.STL
0.015 x 0.024 x 0.015

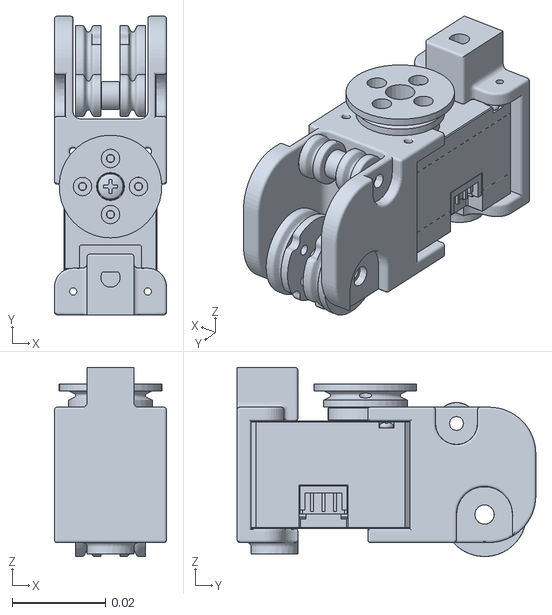
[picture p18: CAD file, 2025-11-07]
DOGlove/DOGlove_meshes/middle_split.STL
0.024 x 0.064 x 0.0405

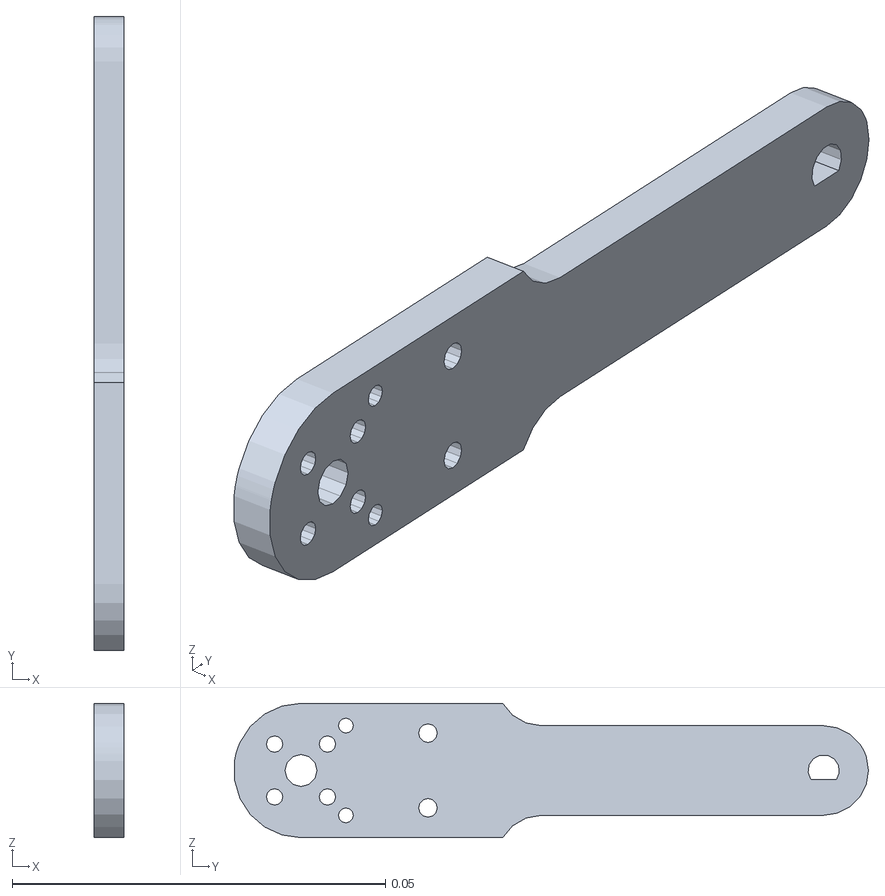
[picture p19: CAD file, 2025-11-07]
DOGlove/DOGlove_meshes/index_bend_3.STL
0.004 x 0.0849 x 0.018

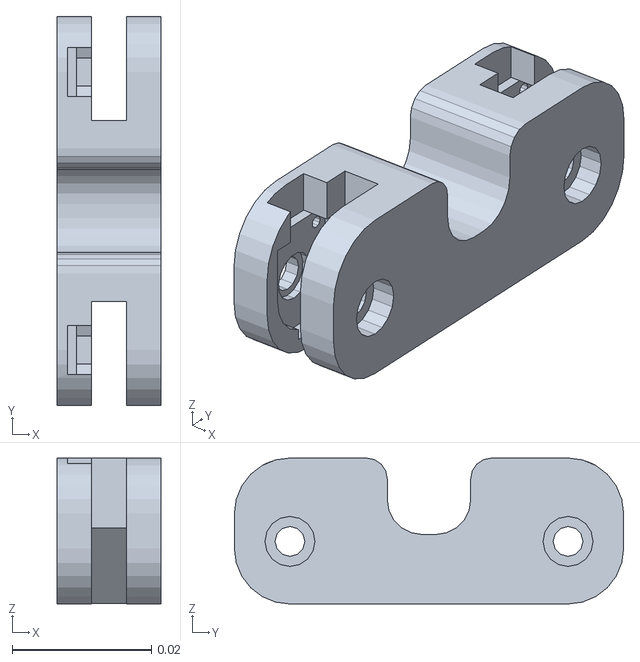
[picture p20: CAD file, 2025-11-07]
DOGlove/DOGlove_meshes/thumb_bend_2.STL
0.015 x 0.056 x 0.021

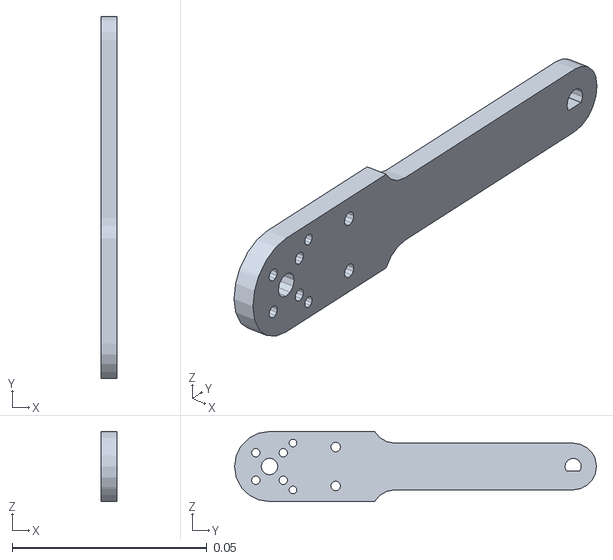
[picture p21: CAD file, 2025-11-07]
DOGlove/DOGlove_meshes/middle_bend_3.STL
0.004 x 0.093 x 0.018

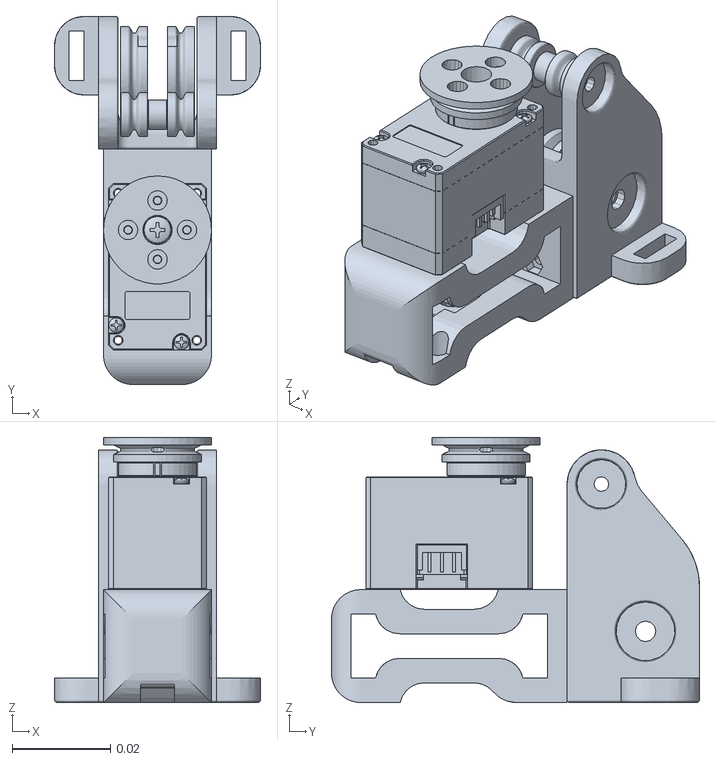
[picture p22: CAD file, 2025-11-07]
DOGlove/DOGlove_meshes/thumb_split.STL
0.042 x 0.075 x 0.054

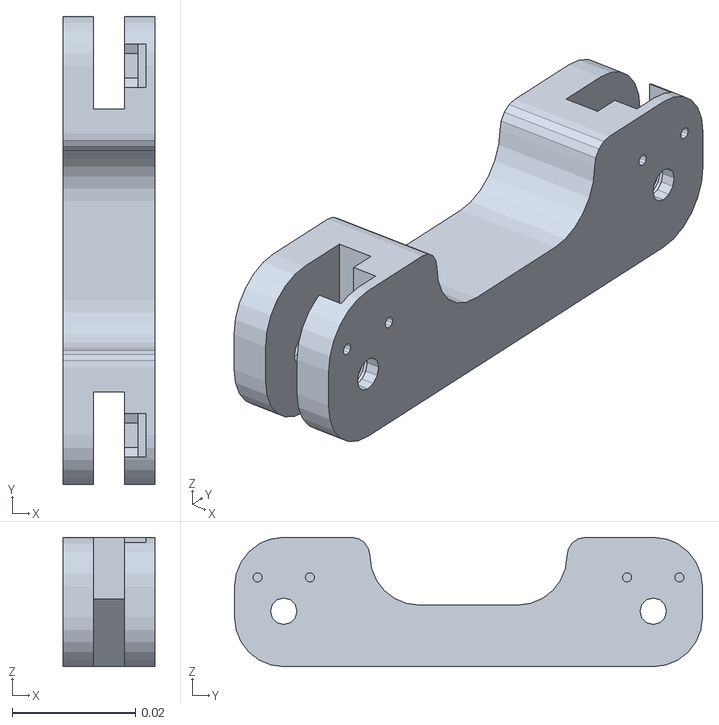
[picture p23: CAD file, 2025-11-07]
DOGlove/DOGlove_meshes/ring_bend_2.STL
0.015 x 0.076 x 0.021

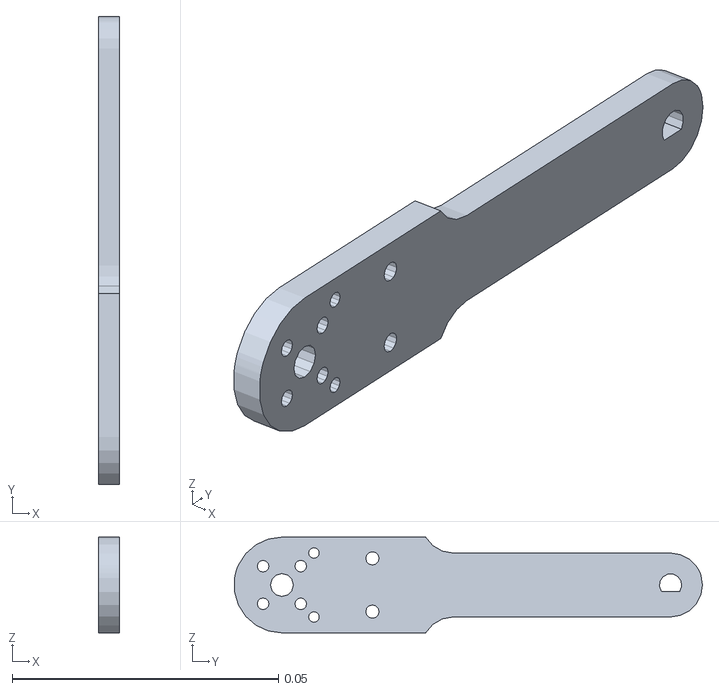
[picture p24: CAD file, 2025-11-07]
DOGlove/DOGlove_meshes/ring_bend_3.STL
0.004 x 0.0879 x 0.018

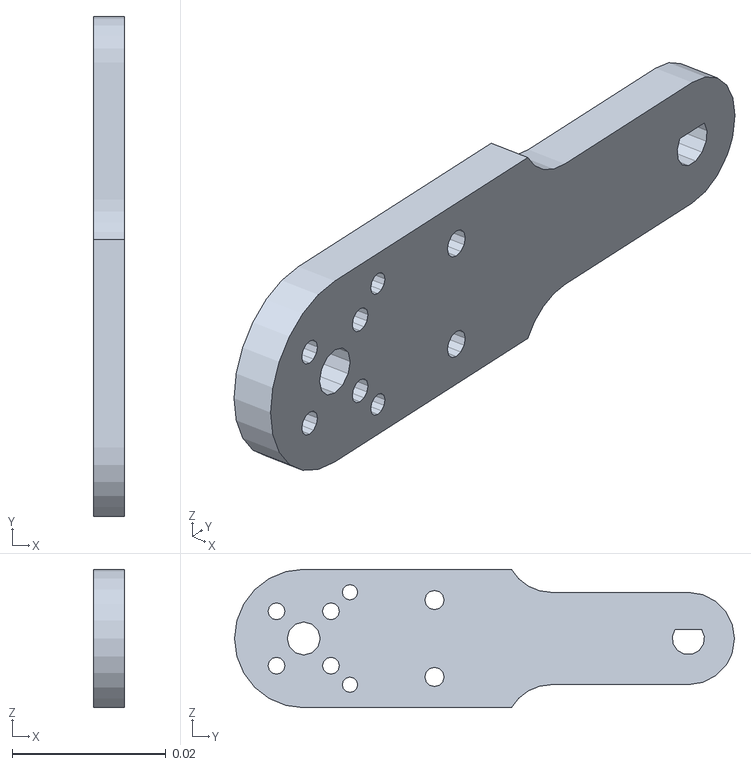
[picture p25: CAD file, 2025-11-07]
DOGlove/DOGlove_meshes/thumb_bend_3.STL
0.004 x 0.065 x 0.018

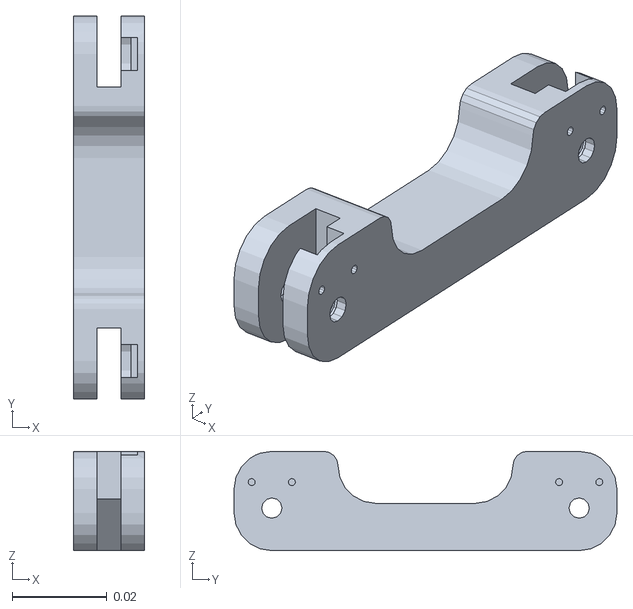
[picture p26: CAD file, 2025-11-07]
DOGlove/DOGlove_meshes/middle_bend_2.STL
0.015 x 0.081 x 0.021

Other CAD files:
DOGlove/DOGlove_meshes/ring_bend_1.STL
DOGlove/DOGlove_meshes/pinky_split.STL
DOGlove/DOGlove_meshes/middle_bend_1.STL
DOGlove/DOGlove_meshes/ring_split.STL
DOGlove/DOGlove_meshes/pinky_bend_1.STL
DOGlove/DOGlove_meshes/thumb_bend_1.STL
DOGlove/DOGlove_meshes/index_bend_2.STL
DOGlove/DOGlove_meshes/index_split.STL
DOGlove/DOGlove_meshes/pinky_bend_3.STL
DOGlove/DOGlove_meshes/thumb_mcp.STL

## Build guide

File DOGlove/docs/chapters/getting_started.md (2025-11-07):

# Getting Started

```{toctree}
:hidden:
:maxdepth: 1

../quick_start/01_pcba.rst
../quick_start/02_3d_print.rst
../quick_start/03_flash_firmware.rst
../quick_start/05_make_it_move.rst
```

## Before You Start

1. Check our [hardware bill of materials (BOM)](#hardware-bill-of-materials) to make sure you have everything.
2. [Order the PCBA](../quick_start/01_pcba).
3. [Print the mechanical structures](../quick_start/02_3d_print).
4. The whole system has been tested under **Ubuntu 20.04**.

(hardware-bill-of-materials)=
## Hardware Bill of Materials

| Component | Quantity | Purchase Link | Purchase Link (China) |
| :--- | ---: | :--- | :--- |
| **3D Print Filament** | | | |
| Bambu PETG Basic (Gold) | 1 |[Bambu Store](https://us.store.bambulab.com/products/petg-hf?id=42735939649672)|[Taobao](https://detail.tmall.com/item.htm?id=816799102364)|
| Bambu PETG HF (White) | 1 |[Bambu Store](https://us.store.bambulab.com/products/petg-hf?id=42735939846280)|[Taobao](https://detail.tmall.com/item.htm?id=816799102364)|
| Bambu Support for PLA/PETG | 1 |[Bambu Store](https://us.store.bambulab.com/products/support-for-pla-petg)|[Taobao](https://detail.tmall.com/item.htm?abbucket=9&id=813808728827)|
| Bambu TPU for AMS (White) | 1 |[Bambu Store](https://us.store.bambulab.com/products/tpu-for-ams?id=43059884720264)|[Taobao](https://detail.tmall.com/item.htm?abbucket=9&id=847975695749&skuId=5633828620351)|
| **Dynamixel Parts** | | | |
| Dynamixel XC330-M288-T | 2 |[Dynamixel Store](https://www.robotis.us/dynamixel-xc330-m288-t/)|<a href="https://item.taobao.com/item.htm?_u=m2pu41081584&id=660146504579&skuId=4941606395637">Taobao</a>|
| Dynamixel XL330-M288-T | 3 |[Dynamixel Store](https://www.robotis.us/dynamixel-xl330-m288-t/)|<a href="https://item.taobao.com/item.htm?_u=m2pu410853f0&id=648175925849">Taobao</a>|
| ROBOTIS U2D2 USB Communication Converter | 1 |[Dynamixel Store](https://www.robotis.us/u2d2/)|<a href="https://item.taobao.com/item.htm?_u=m2pu4108eef4&id=564915402895">Taobao</a>|
| ROBOTIS Cable-X3P 100mm | 4 |Temporarily unavailable (non-critical)|<a href="https://item.taobao.com/item.htm?_u=m2pu41088bc7&id=559824480883&skuId=3659974074027">Taobao</a>|
| **Mechanical Parts** | | | |
| M2x10mm Button Head Screw | 12 |[97763A409](https://www.mcmaster.com/97763A409/)|[M2x10十字圆头](https://detail.tmall.com/item.htm?abbucket=9&id=637524754721&skuId=4742801506990)|
| M2x12mm Button Head Screw | 10 |[92095A455](https://www.mcmaster.com/92095A455/)|[M2x12十字圆头](https://detail.tmall.com/item.htm?abbucket=9&id=637524754721&skuId=4742801506984)|
| M2x20+3mm Single Through Copper Standoff | 1 |[Amazon](https://www.amazon.com/ZZHXSM-320PCS-Hexagonal-Motherboard-Computer/dp/B0DHKTWMPH/)|[M2x20+3单通滚花铜柱](https://detail.tmall.com/item.htm?abbucket=9&id=534855987272&skuId=5775647192461)|
| M2x20mm Dual Through Copper Standoff | 1 |[As provided above](https://www.amazon.com/ZZHXSM-320PCS-Hexagonal-Motherboard-Computer/dp/B0DHKTWMPH/)|[M2x20双通滚花铜柱](https://detail.tmall.com/item.htm?abbucket=9&id=534855987272&skuId=5942557358119)|
| M2x5mm Self-Tapping Screw | 20 |[90380A325](https://www.mcmaster.com/90380A325/)|[M2x5十字圆头割尾自攻](https://detail.tmall.com/item.htm?abbucket=9&id=535345606154&skuId=4327300926628)|
| M2x6mm Self-Tapping Screw | 16 |(From servo box)|(From servo box)|
| M2x8mm Self-Tapping Screw | 20 |(From servo box)|(From servo box)|
| M2x5x0.3mm Washer | 12 |[Amazon](https://www.amazon.com/Washers-Stainless-Assortment-Sizes%EF%BC%88M2-Industrial/dp/B0CBJZNDN4/)|[M2x5x0.3平垫片](https://detail.tmall.com/item.htm?abbucket=9&id=736651447364&skuId=5800439948793)|
| M2 Lock Nut | 10 |[Amazon](https://www.amazon.com/M2-0-3-Insert-Locknuts-Stainless-Clinching/dp/B0DR93VFYG/)|[M2防松螺母](https://detail.tmall.com/item.htm?abbucket=9&id=763443678130&skuId=5254837848373)|
| M2 Hex Nut | 10 |[90592A075](https://www.mcmaster.com/90592A075/)|[M2六角螺母](https://detail.tmall.com/item.htm?abbucket=9&id=549640610734&skuId=3507734575864)|
| M3x10mm Button Head Screw | 2 |[92095A182](https://www.mcmaster.com/92095A182/)|[M3x10十字圆头](https://detail.tmall.com/item.htm?abbucket=9&id=637524754721&skuId=4742801506977)|
| M3x30mm Button Head Screw | 2 |[92095A187](https://www.mcmaster.com/92095A187/)|[M3x30十字圆头](https://detail.tmall.com/item.htm?abbucket=9&id=637524754721&skuId=4742801506999)|
| M3x15mm D-Shape Shaft Screw | 16 | — |<a href="https://item.taobao.com/item.htm?ft=t&id=935960628369">Purchase directly from factory</a>|
| M3x20mm Dual Through Copper Standoff | 2 |[Amazon](https://www.amazon.com/Csdtylh-Male-Female-Standoff-Stainless-Assortment/dp/B06Y5TJXY1/)|[M3x20双通铜柱](https://detail.tmall.com/item.htm?abbucket=9&id=542213588710&skuId=3258324297349)|
| M3 Lock Nut | 12 |[Amazon](https://www.amazon.com/Yinpecly-Stainless-Self-Locking-Industrial-Construction/dp/B0F1MSSVQP/)|[M3防松螺母](https://detail.tmall.com/item.htm?abbucket=9&id=763443678130&skuId=5740530721046)|
| M4x10mm Button Head Screw | 14 |[92095A190](https://www.mcmaster.com/92095A190/)|[M4x10十字圆头](https://detail.tmall.com/item.htm?abbucket=9&id=637524754721&skuId=4742801506971)|
| M4x15mm Dual Through Copper Standoff | 4 |[Amazon](https://www.amazon.com/Standoff-Motherboard-Hexagon-Spacer-Assortment/dp/B09X358Q73/)|[M4x15双通铜柱](https://detail.tmall.com/item.htm?abbucket=9&id=542213588710&skuId=4348642093877)|
| M4x20mm Dual Through Copper Standoff | 1 |[As provided above](https://www.amazon.com/Standoff-Motherboard-Hexagon-Spacer-Assortment/dp/B09X358Q73/)|[M4x20双通铜柱](https://detail.tmall.com/item.htm?abbucket=9&id=542213588710&skuId=4348642093875)|
| M4 Thin-Profile Hex Nut | 4 |[90710A035](https://www.mcmaster.com/90710A035/)|[M4扁薄六角螺母](https://detail.tmall.com/item.htm?_u=m2pu410880c4&id=533915610076&skuId=4937683182274)|
| 7x4x2.5mm Bearing | 16 |[Amazon](https://www.amazon.com/uxcell-Bearings-4x7x2-5mm-Miniature-Precision/dp/B0CM6RYCC7/)|[MR74-ZZ P5【4x7x2.5】轴承](https://detail.tmall.com/item.htm?_u=m2pu41088525&id=743100333785&skuId=5123565292062)|
| 0.6mm 7x7 Stainless Steel Wire Rope | 25ft / 10m |[3461T07](https://www.mcmaster.com/3461T07/)|<a href="https://item.taobao.com/item.htm?_u=m2pu4108c68a&id=574480300292&skuId=3929526017813">钢丝绳</a>|
| M3x25mm Headless Clevis Pin | 5 |[93890A703](https://www.mcmaster.com/93890A703/)|[M3x25双头卡簧销轴](https://detail.tmall.com/item.htm?_u=m2pu41084dab&id=755183277159&skuId=5205582448931)|
| M2 Circlip | 10 |[Amazon](https://www.amazon.com/Circlip-External-Retaining-Stainless-Assortment/dp/B0BNB39FKY/)|[M2-e型卡簧挡圈](https://detail.tmall.com/item.htm?_u=m2pu41083fee&id=557748539457&skuId=5002991824253)|
| M4x25mm Headless Clevis Pin | 5 |[93890A707](https://www.mcmaster.com/93890A707/)|[M4x25双头卡簧销轴](https://detail.tmall.com/item.htm?_u=m2pu41084dab&id=755183277159&skuId=5205582448938)|
| M3 Circlip | 10 |[As provided above](https://www.amazon.com/Circlip-External-Retaining-Stainless-Assortment/dp/B0BNB39FKY/)|[M3-e型卡簧挡圈](https://detail.tmall.com/item.htm?_u=m2pu41083fee&id=557748539457&skuId=4902892140873)|
| **Electronics** | | | |
| RDC506 Encoder | 16 |[DigiKey](https://www.digikey.com/en/products/detail/alps-alpine/RDC506018A/19529120), [Mouser](https://www.mouser.com/ProductDetail/Alps-Alpine/RDC506018A?qs=j%252B1pi9TdxUZl0Obrq5eEAQ%3D%3D)|[LCSC-RDC506002A](https://item.szlcsc.com/116589.html), [LCSC-RDC506018A](https://item.szlcsc.com/364160.html)|
| LRA0825 Haptic Motor | 5 |[JYLRA0825Z](https://www.digikey.com/en/products/detail/jie-yi-electronics-limited/JYLRA0825Z/22519426), [LRA0825BC-0167F](https://www.digikey.com/en/products/detail/ineed-motor/LRA0825BC-0167F/21840080)|[LCSC-LD0825BC-0169F](https://item.szlcsc.com/6552539.html)|
| USB to TTL Module | 1 |[Amazon](https://www.amazon.com/JESSINIE-Module-CH343-Communication-Microcontroller/dp/B0D6352BS9/)|<a href="https://item.taobao.com/item.htm?_u=m2pu41088297&id=674671646143&skuId=4849832708260">nanoUART</a>|
| **Cables** | | | |
| PH2.0 Pre-Crimped Wire, 15cm (R/Y/B) | 6 |[Amazon](https://www.amazon.com/Yoeruyo-PH2-0mm-Connector-Pre-Crimped-3Pin-100CM/dp/B0C2HHHNX9/)|<a href="https://item.taobao.com/item.htm?_u=m2pu4108e868&id=596387029707&skuId=4317745623497">PH2.0镀金单头端子线，电子线15cm，红/黄/黑</a>|
| PH2.0 Pre-Crimped Wire, 25cm (R/Y/B) | 5 |[Amazon](https://www.amazon.com/Yoeruyo-PH2-0mm-Connector-Pre-Crimped-3Pin-100CM/dp/B0C2HBL668/)|<a href="https://item.taobao.com/item.htm?_u=m2pu4108e868&id=596387029707&skuId=4317745623533">PH2.0镀金单头端子线，电子线25cm，红/黄/黑</a>|
| PH2.0 Pre-Crimped Wire, 30cm (R/Y/B) | 5 |[Amazon](https://www.amazon.com/Yoeruyo-PH2-0mm-Connector-Pre-Crimped-3Pin-100CM/dp/B0C2HBL668/)|<a href="https://item.taobao.com/item.htm?_u=m2pu4108e868&id=596387029707&skuId=4317745623533">PH2.0镀金单头端子线，电子线30cm，红/黄/黑</a>|
| PH2.0-3P Housing | 16 |As provided above|<a href="https://item.taobao.com/item.htm?id=15486830256&spm=a1z09.2.0.0.6b202e8dOSJ2GK&skuId=3283156525609">PH2.0-3P胶壳</a>|
| SH1.0 Pre-Crimped Wire, 40cm (R/B) | 5 |[Amazon](https://www.amazon.com/Cermant-SH1-0mm-Pin-Connector-Female/dp/B0DM238Y63/)|<a href="https://item.taobao.com/item.htm?_u=m2pu41080c07&id=595880379976&skuId=4302450046792">SH1.0镀金单头端子线，特软硅胶线40cm，红/黑</a>|
| SH1.0-2P Housing | 5 |As provided above|<a href="https://item.taobao.com/item.htm?_u=m2pu41087701&id=595859715531&skuId=4132094928761">SH1.0-2P胶壳</a>|
| USB-A to MicroUSB Cable, 3m | 1 |[Amazon](https://www.amazon.com/MaGeek-Premium-Samsung-Motorola-Google/dp/B00WEVG57K/)|[JD](https://item.jd.com/100039185783.html)|
| USB-A to Type-C Cable, 3m | 1 |[Amazon](https://www.amazon.com/Belkin-BoostCharge-Samsung-Nintendo-Carplay/dp/B08558DD7G/)|[JD](https://item.jd.com/100008391172.html)|
| **Programming Tools** | | | |
| ST-Link V2 Downloader | 1 |[Amazon](https://www.amazon.com/AITRIP-Emulator-Downloader-Programmer-STM32F103C8T6/dp/B0D22S8WVX/)|[ST-Link V2下载器](https://detail.tmall.com/item.htm?abbucket=9&id=558866168716&skuId=5146051183964)|
| 2.54-4p Pin Header | 1 |[Amazon](https://www.amazon.com/Jabinco-Breakable-Header-Connector-Arduino/dp/B0817JG3XN/)|[2.54-4p单排针](https://detail.tmall.com/item.htm?abbucket=9&id=546772885976&skuId=3398671888945)|
| Dupont Cable F/F | 4 |[Amazon](https://www.amazon.com/California-JOS-Breadboard-Optional-Multicolored/dp/B0BRTJXND9/)|[杜邦线母对母](https://detail.tmall.com/item.htm?abbucket=9&id=41254478179&skuId=5755030488371)|
| **Power Supply** | | | |
| MEAN Well RSP-320-5V Power Supply | 1 |[Amazon](https://www.amazon.com/Mean-RSP-320-5-Power-Supply-Signs/dp/B00IWC2RLS/)|[明纬RSP-320-5V](https://detail.tmall.com/item.htm?_u=i2pu41088bc7&id=547752759011&skuId=4572439414905)|
| Emergency Stop Button | 1 |[Amazon](https://www.amazon.com/Emergency-Button-Momentary-PushButton-Switches/dp/B0CWV7L81B/)|[施耐德XALJ01C急停开关](https://item.jd.com/100114884831.html)|
| Power Cord (Type I, 2m) | 1 |[Amazon](https://www.amazon.com/StarTech-com-NEMA-Power-Cord-Volts/dp/B002VY53QE/)|[品字电源线](https://item.jd.com/100132121492.html)|
| **Accessories** | | | |
| UV Resin Glue | 1 |[Amazon](https://www.amazon.com/dp/B0BJ65T85R/)|[Ergo 8500](https://item.jd.com/100045475837.html)|
| Super Glue | 1 |[Amazon](https://www.amazon.com/Scotch-Super-Liquid-Ounces-AD114/dp/B001PILFVY/)|[Ergo 5910](https://item.jd.com/100198857334.html)|
| Zip Tie 2.5mmx15cm | 50 |[Amazon](https://www.amazon.com/KOOWIN-Small-Nylon-Plastic-Cable/dp/B08HMPBY3L/)|[扎带2.5x200mm](https://item.jd.com/100023555528.html)|
| Cable Ties Reusable 9mmx15cm | 6 |[Amazon](https://www.amazon.com/CableCreation-Fastening-Organizer-Adjustable-Management/dp/B07CWLHRQP/)|[魔术贴9mm*15cm](https://item.jd.com/100002860615.html)|
| Hook and Loop Reusable Fastening Cable Tie 20mmx20cm | 1 |[Amazon](https://www.amazon.com/Inches-Reusable-Fastening-Straps-Wisdompro/dp/B01M1L1YHO/)|[带扣魔术贴20mm*25cm](https://item.jd.com/100120892220.html)|

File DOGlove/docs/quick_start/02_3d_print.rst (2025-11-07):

3D Printing Guide
===================

This guide is optimized for the **Bambu P1S Combo (P1SC)** printer using official Bambu filaments.

Materials List
--------------

.. list-table::
   :header-rows: 1
   :widths: 30 10 30 30

   * - Component
     - Quantity
     - Purchase Link
     - Purchase Link (China)
   * - **3D Print Filament**
     - 
     - 
     - 
   * - Bambu PETG Basic (Gold)
     - 1
     - `Bambu PETG Basic Gold <https://us.store.bambulab.com/products/petg-hf?id=42735939649672>`_
     - `Taobao PETG Basic <https://detail.tmall.com/item.htm?id=816799102364>`_
   * - Bambu PETG HF (White)
     - 1
     - `Bambu PETG HF White <https://us.store.bambulab.com/products/petg-hf?id=42735939846280>`_
     - `Taobao PETG HF <https://detail.tmall.com/item.htm?id=816799102364>`_
   * - Bambu Support for PLA/PETG
     - 1
     - `Bambu Support <https://us.store.bambulab.com/products/support-for-pla-petg>`_
     - `Taobao Support <https://detail.tmall.com/item.htm?abbucket=9&id=813808728827>`_
   * - Bambu TPU for AMS (White)
     - 1
     - `Bambu TPU <https://us.store.bambulab.com/products/tpu-for-ams?id=43059884720264>`_
     - `Taobao TPU <https://detail.tmall.com/item.htm?abbucket=9&id=847975695749&skuId=5633828620351>`_

Printing with Bambu Studio
--------------------------

If you're using a Bambu printer:

#. Visit our `MakerWorld model page <https://makerworld.com/en/models/1476400-doglove#profileId-1541008>`_.
#. Click **Open in Bambu Studio**.
#. Match the filament colors with those loaded in your AMS.
#. Start the print.

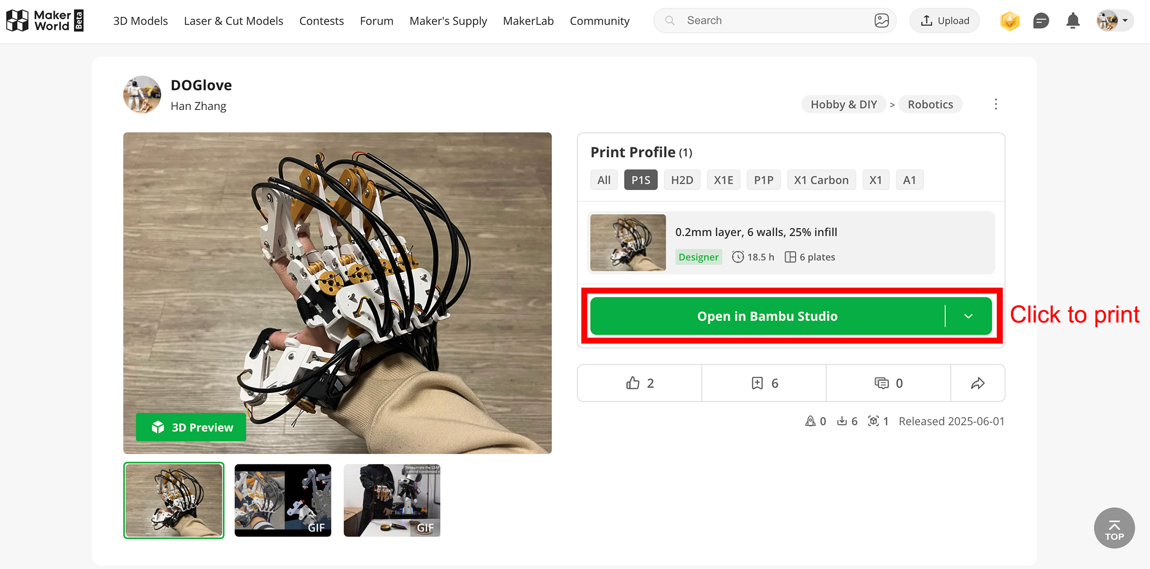
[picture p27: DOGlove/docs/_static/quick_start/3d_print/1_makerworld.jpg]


.. tip::

   We recommend using **Bambu Liquid Glue for Build Plate** to improve first-layer adhesion.

   `Buy here <https://us.store.bambulab.com/products/liquid-glue-for-build-plate>`_, `购买链接 <https://detail.tmall.com/item.htm?abbucket=13&detail_redpacket_pop=true&id=698882119427>`_

.. note::

   Bambu PETG Basic (Gold) may be out of stock.

   You can substitute it with Bambu PETG HF (Yellow) or any other PETG HF color of your choice.

Printing on Non-Bambu Printers
------------------------------

For users of other 3D printers, here are some material and profile suggestions:

- **Joints & Fingers**: PETG

  - Use a strong-print profile: 50% sparse infill, 50% infill/wall overlap, 10 wall loops

- **Palm**: PETG or PLA

  - Use a standard print profile: low infill density and fewer wall loops to reduce weight

- **TPU Components**: Use the softest TPU possible for comfort when contacting the skin

.. note::

   Bambu AMS supports TPU 68D.

   If your printer allows, consider softer filaments like TPU 90A or TPU 85A.

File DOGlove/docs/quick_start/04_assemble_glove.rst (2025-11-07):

# Glove Assembly
1. Prepare the cables
./cable.mp4

2. Solder the encoders
./encoder.mp4

[Notice:] For soldering tips, you may check [YouTube] tutorials.

3. Assemble the index/middle/ring/pinky joint

4. Assemble the thumb joint

5. Assemble the palm

6. Wrap the cable

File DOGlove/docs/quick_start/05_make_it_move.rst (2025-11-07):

.. _make_it_move:

================
Make It Move
================

1. Wire Connection
====================

**Encoder Connection**
-------------------------

Follow the image tutorial below to connect the joint encoders to the corresponding board connector.

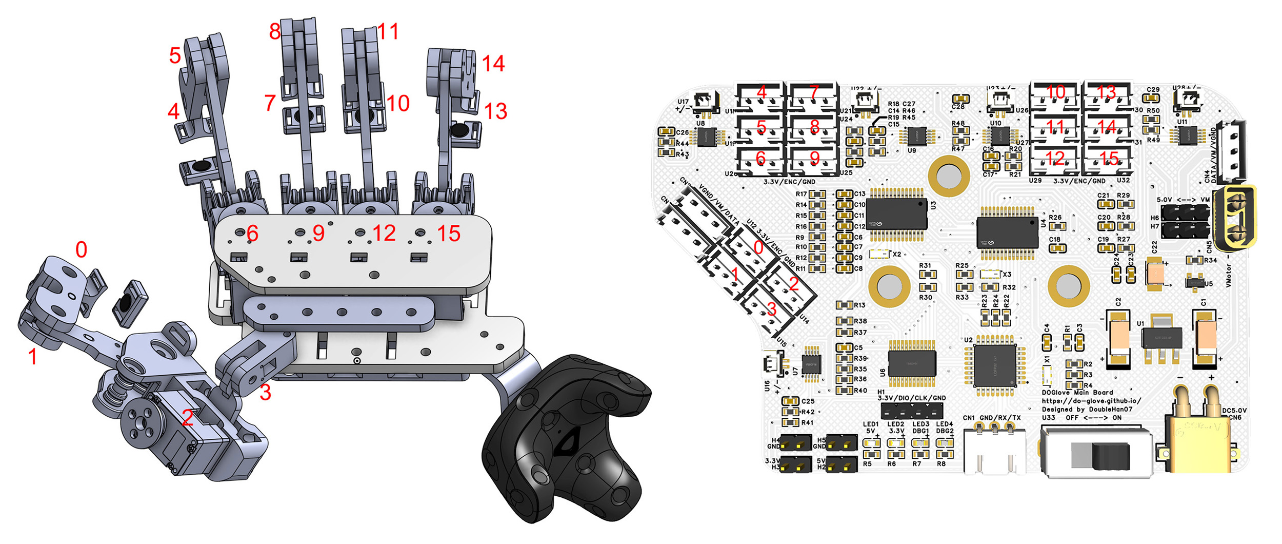
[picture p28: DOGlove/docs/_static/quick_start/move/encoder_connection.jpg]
Encoder Connection


.. note::
   You should strictly follow the number allocation in the image, otherwise the joint mapping will be incorrect.

**Servo Connection**
-----------------------

The Dynamixel servo supports chain connection.

Simply connect the index, middle, ring, and pinky servos together, then use one cable to connect the four servos to **CN2** on the main board. Connect the thumb servo to **CN3** on the main board.

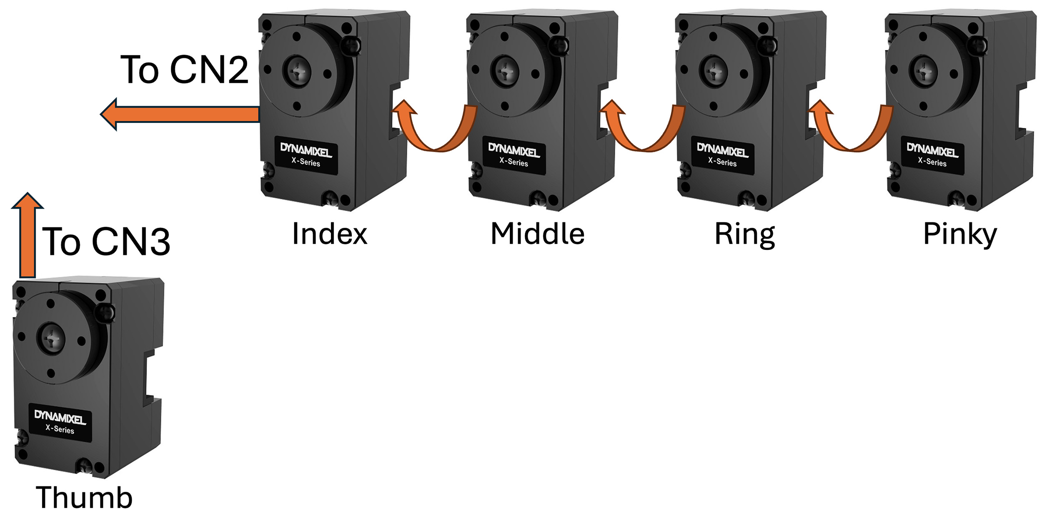
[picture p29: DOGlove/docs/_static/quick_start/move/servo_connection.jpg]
Servo Connection


Then connect Dynamixel U2D2 to **CN4**.

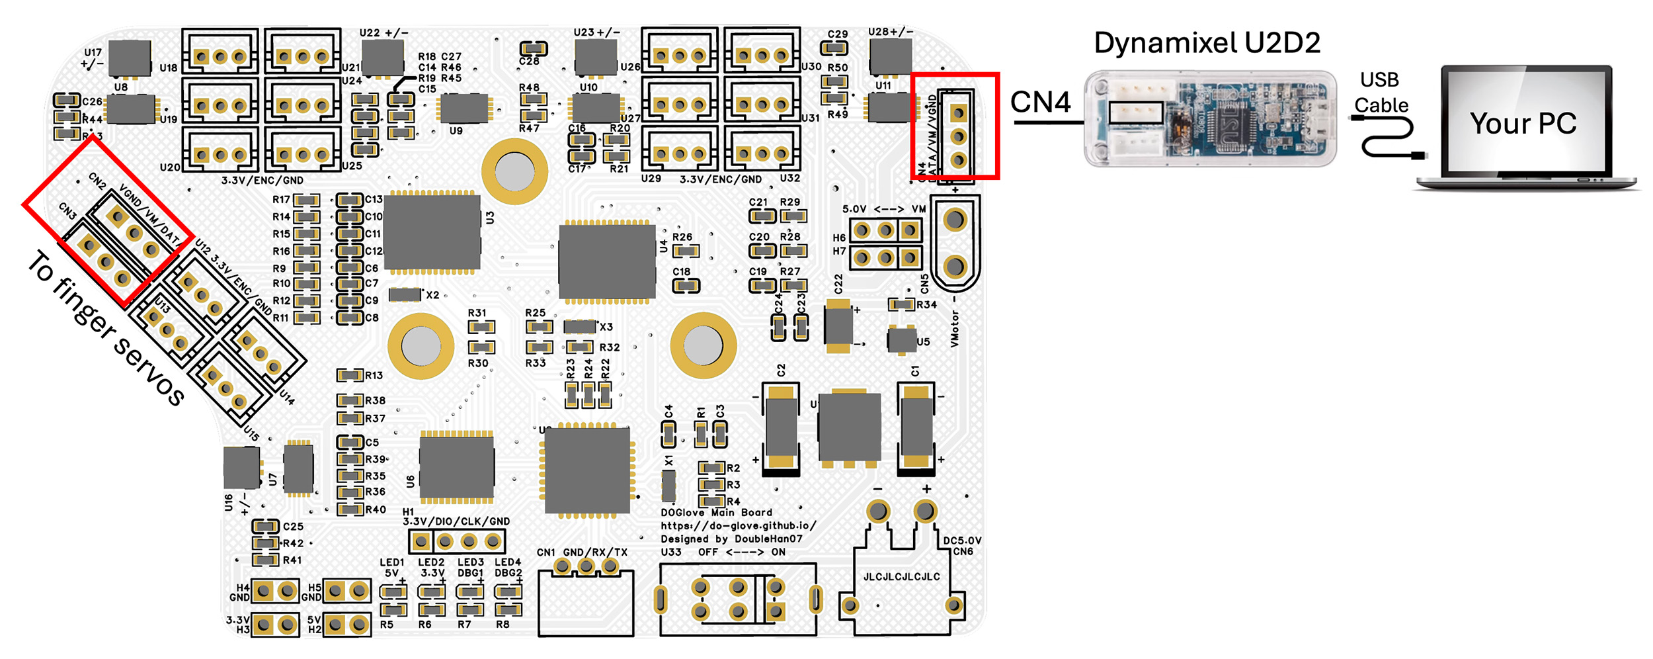
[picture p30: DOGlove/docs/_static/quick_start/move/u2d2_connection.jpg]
U2D2 Connection


**Power Tree**
-----------------

The board is powered by DC 5.0V.

If you use the recommended power supply (`MEAN Well RSP-320-5V Power Supply <../chapters/getting_started.html>`_), simply **short the left two pins of H6 and H7**. 

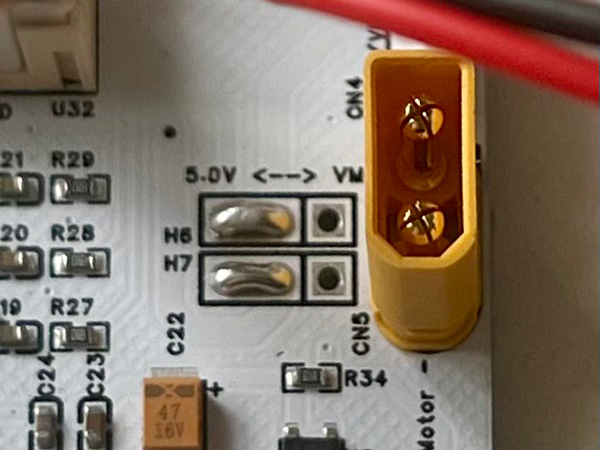
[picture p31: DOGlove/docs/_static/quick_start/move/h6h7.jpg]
H6 H7 Jumper


This way, both the digital circuit and servos are powered from a single power input CN6. CN6 is an XT30 Male connector.

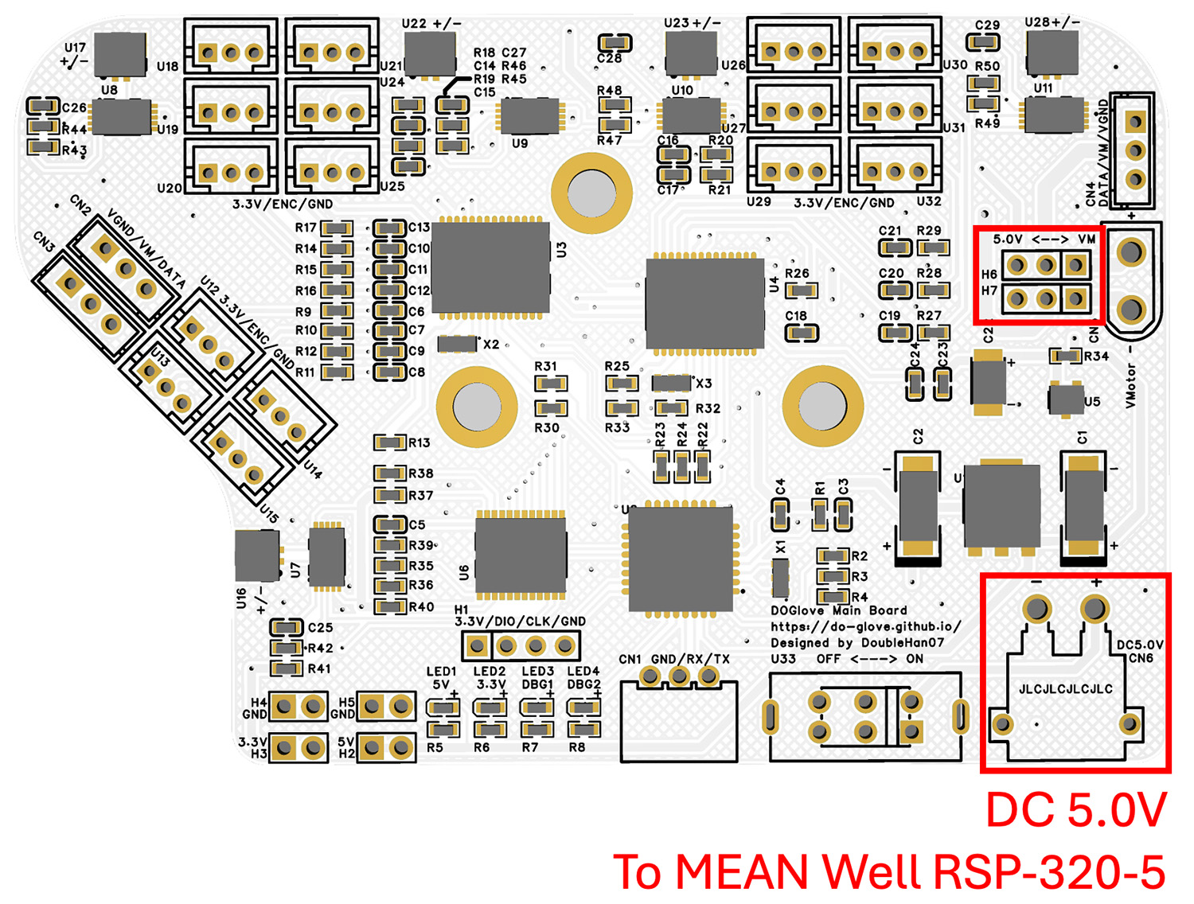
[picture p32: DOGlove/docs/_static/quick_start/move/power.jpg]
Power Tree


.. note::
   H6 and H7 select the power source for the servos. 

   Short the **left two pins** to power the servos from CN6 (same source as the MCU).
   
   Short the **right two pins** to power the servos independently from CN5.

This design allows you to separate the power supply for the servos and MCU if needed (e.g., when your power supply cannot provide sufficient current for servo stall current).

2. Status LED Check
======================

Hurray! It's time to power on the whole system!

Turn on the switch **U33** on the main board. If everything is functioning properly, all the status LEDs should light up.

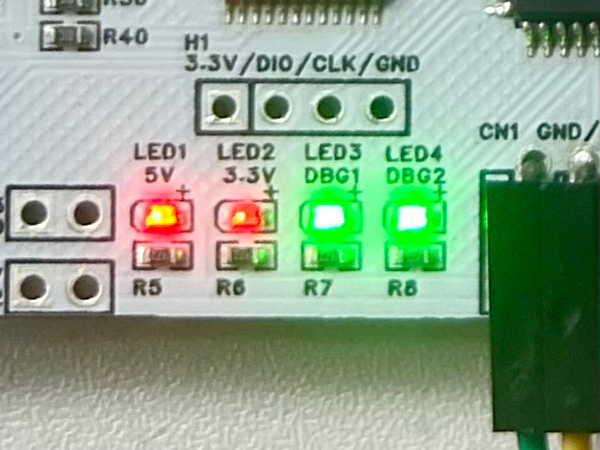
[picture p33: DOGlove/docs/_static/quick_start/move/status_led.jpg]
Status LED


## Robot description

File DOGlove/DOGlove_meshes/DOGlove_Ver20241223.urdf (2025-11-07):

<?xml version="1.0" encoding="utf-8"?>
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
<robot name="DOGlove_Ver20241223">
  <link name="base_link">
    <inertial>
      <origin xyz="-0.0240239529110336 -0.016382201418219 -0.0238366502311693" rpy="0 0 0" />
      <mass value="0.185697083197622" />
      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
    </inertial>
    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
  </link>
  <link name="index_split">
    <inertial>
      <origin xyz="2.01866500437742E-06 0.0196178970011489 -0.0272426373843988" rpy="0 0 0" />
      <mass value="0.0331994485719628" />
      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
    </inertial>
    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
  </link>
  <joint name="index_split" type="revolute">
    <origin xyz="-0.0849999999999999 -0.0601040764008531 -0.104852813742388" rpy="-1.5707963267949 -0.785398163397448 1.5707963267949" />
    <parent link="base_link" />
    <child link="index_split" />
    <axis xyz="0 0 1" />
    <limit lower="0" upper="0.436" effort="0" velocity="0" />
  </joint>
  <link name="index_bend_3">
    <inertial>
      <origin xyz="-1.16573417585641E-15 0.0302786278809853 -3.00020989626656E-06" rpy="0 0 0" />
      <mass value="0.00454937532002053" />
      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
    </inertial>
    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
  </link>
  <joint name="index_bend_3" type="revolute">
    <origin xyz="0 0.045 -0.0365" rpy="0 0 0" />
    <parent link="index_split" />
    <child link="index_bend_3" />
    <axis xyz="1 0 0" />
    <limit lower="0" upper="1.16" effort="0" velocity="0" />
  </joint>
  <link name="index_bend_2">
    <inertial>
      <origin xyz="-0.000180674798107489 0.0299999999999998 -0.000190738564997725" rpy="0 0 0" />
      <mass value="0.013291543115275" />
      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
    </inertial>
    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
  </link>
  <joint name="index_bend_2" type="revolute">
    <origin xyz="0 0.07 0" rpy="0 0 0" />
    <parent link="index_bend_3" />
    <child link="index_bend_2" />
    <axis xyz="1 0 0" />
    <limit lower="-2.61" upper="0" effort="0" velocity="0" />
  </joint>
  <link name="index_bend_1">
    <inertial>
      <origin xyz="-1.11022302462516E-16 0.00880991685622767 -1.91166527052644E-15" rpy="0 0 0" />
      <mass value="0.00133489669454765" />
      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
    </inertial>
    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
  </link>
  <joint name="index_bend_1" type="revolute">
    <origin xyz="0 0.06 0" rpy="0 0 0" />
    <parent link="index_bend_2" />
    <child link="index_bend_1" />
    <axis xyz="1 0 0" />
    <limit lower="-2.09" upper="0" effort="0" velocity="0" />
  </joint>
  <link name="middle_split">
    <inertial>
      <origin xyz="2.0201686107002E-06 0.0196179022547952 -0.027242637384398" rpy="0 0 0" />
      <mass value="0.0331994485719631" />
      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
    </inertial>
    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
  </link>
  <joint name="middle_split" type="revolute">
    <origin xyz="-0.0849999999999999 -0.0417193000900034 -0.0864680374315374" rpy="-1.5707963267949 -0.785398163397448 1.5707963267949" />
    <parent link="base_link" />
    <child link="middle_split" />
    <axis xyz="0 0 1" />
    <limit lower="-0.087" upper="0.2615" effort="0" velocity="0" />
  </joint>
  <link name="middle_bend_3">
    <inertial>
      <origin xyz="6.19643225618915E-14 0.0339728289866728 -2.7666748464647E-06" rpy="0 0 0" />
      <mass value="0.00493337532002052" />
      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
    </inertial>
    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
  </link>
  <joint name="middle_bend_3" type="revolute">
    <origin xyz="0 0.045 -0.0365" rpy="0 0 0" />
    <parent link="middle_split" />
    <child link="middle_bend_3" />
    <axis xyz="1 0 0" />
    <limit lower="0" upper="1.15" effort="0" velocity="0" />
  </joint>
  <link name="middle_bend_2">
    <inertial>
      <origin xyz="-0.000171024427178729 0.0325000000110407 -0.000394202382995382" rpy="0 0 0" />
      <mass value="0.014041543115275" />
      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
    </inertial>
    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
  </link>
  <joint name="middle_bend_2" type="revolute">
    <origin xyz="0 0.078 0" rpy="0 0 0" />
    <parent link="middle_bend_3" />
    <child link="middle_bend_2" />
    <axis xyz="1 0 0" />
    <limit lower="-2.44" upper="0" effort="0" velocity="0" />
  </joint>
  <link name="middle_bend_1">
    <inertial>
      <origin xyz="6.32410790402105E-14 0.0088099168675338 7.75712480360902E-12" rpy="0 0 0" />
      <mass value="0.00133489669454766" />
      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
    </inertial>
    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
  </link>
  <joint name="middle_bend_1" type="revolute">
    <origin xyz="0 0.065 0" rpy="0 0 0" />
    <parent link="middle_bend_2" />
    <child link="middle_bend_1" />
    <axis xyz="1 0 0" />
    <limit lower="-2.09" upper="0" effort="0" velocity="0" />
  </joint>
  <link name="ring_split">
    <inertial>
      <origin xyz="2.01959282369879E-06 0.0196179008908676 -0.0272426373843986" rpy="0 0 0" />
      <mass value="0.0331994485719624" />
      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
    </inertial>
    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
  </link>
  <joint name="ring_split" type="revolute">
    <origin xyz="-0.085 -0.0233345237791538 -0.0680832611206866" rpy="-1.5707963267949 -0.785398163397448 1.5707963267949" />
    <parent link="base_link" />
    <child link="ring_split" />
    <axis xyz="0 0 1" />
    <limit lower="-0.1045" upper="0.052" effort="0" velocity="0" />
  </joint>
  <link name="ring_bend_3">
    <inertial>
      <origin xyz="0 0.0316580893023667 -2.90815882332887E-06" rpy="0 0 0" />
      <mass value="0.00469337532002052" />
      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
    </inertial>
    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
  </link>
  <joint name="ring_bend_3" type="revolute">
    <origin xyz="0 0.045 -0.0365" rpy="0 0 0" />
    <parent link="ring_split" />
    <child link="ring_bend_3" />
    <axis xyz="1 0 0" />
    <limit lower="0" upper="1.15" effort="0" velocity="0" />
  </joint>
  <link name="ring_bend_2">
    <inertial>
      <origin xyz="-0.000180674798105157 0.03 -0.000190738564995879" rpy="0 0 0" />
      <mass value="0.013291543115275" />
      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
    </inertial>
    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
  </link>
  <joint name="ring_bend_2" type="revolute">
    <origin xyz="0 0.073 0" rpy="0 0 0" />
    <parent link="ring_bend_3" />
    <child link="ring_bend_2" />
    <axis xyz="1 0 0" />
    <limit lower="-2.61" upper="0" effort="0" velocity="0" />
  </joint>
  <link name="ring_bend_1">
    <inertial>
      <origin xyz="-4.16333634234434E-16 0.00880991685622662 -7.35522753814166E-16" rpy="0 0 0" />
      <mass value="0.00133489669454765" />
      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
    </inertial>
    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
  </link>
  <joint name="ring_bend_1" type="revolute">
    <origin xyz="0 0.06 0" rpy="0 0 0" />
    <parent link="ring_bend_2" />
    <child link="ring_bend_1" />
    <axis xyz="1 0 0" />
    <limit lower="-2.09" upper="0" effort="0" velocity="0" />
  </joint>
  <link name="pinky_split">
    <inertial>
      <origin xyz="2.02065542823787E-06 0.0196179032776091 -0.027242633824687" rpy="0 0 0" />
      <mass value="0.0331994485719634" />
      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
    </inertial>
    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
  </link>
  <joint name="pinky_split" type="revolute">
    <origin xyz="-0.085 -0.0049497 -0.049698" rpy="-1.5708 -0.7854 1.5708" />
    <parent link="base_link" />
    <child link="pinky_split" />
    <axis xyz="0 0 1" />
    <limit lower="-0.227" upper="0" effort="0" velocity="0" />
  </joint>
  <link name="pinky_bend_3">
    <inertial>
      <origin xyz="-5.64825963778048E-15 0.0279974271067274 -3.16729908511268E-06" rpy="0 0 0" />
      <mass value="0.00430937532002052" />
      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
    </inertial>
    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
  </link>
  <joint name="pinky_bend_3" type="revolute">
    <origin xyz="0 0.045 -0.0365" rpy="0 0 0" />
    <parent link="pinky_split" />
    <child link="pinky_bend_3" />
    <axis xyz="1 0 0" />
    <limit lower="0" upper="1.14" effort="0" velocity="0" />
  </joint>
  <link name="pinky_bend_2">
    <inertial>
      <origin xyz="-0.000191479377526345 0.0275000000000266 3.70600440735037E-05" rpy="0 0 0" />
      <mass value="0.012541543115275" />
      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
    </inertial>
    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
  </link>
  <joint name="pinky_bend_2" type="revolute">
    <origin xyz="0 0.065 0" rpy="0 0 0" />
    <parent link="pinky_bend_3" />
    <child link="pinky_bend_2" />
    <axis xyz="1 0 0" />
    <limit lower="-2.44" upper="0" effort="0" velocity="0" />
  </joint>
  <link name="pinky_bend_1">
    <inertial>
      <origin xyz="-9.08995101411847E-16 0.00880991685622626 -2.65412691824451E-15" rpy="0 0 0" />
      <mass value="0.00133489669454765" />
      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
    </inertial>
    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
  </link>
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

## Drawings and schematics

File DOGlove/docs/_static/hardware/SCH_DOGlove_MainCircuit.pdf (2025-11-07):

# 5V-3.3V LDO

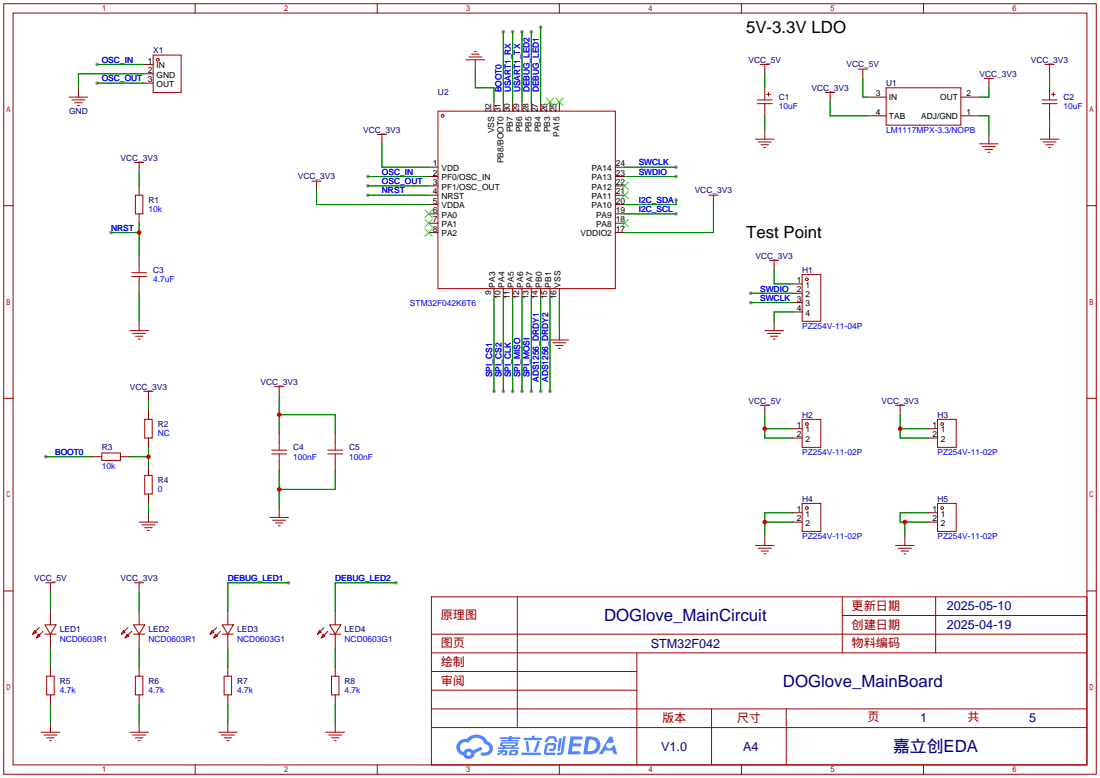
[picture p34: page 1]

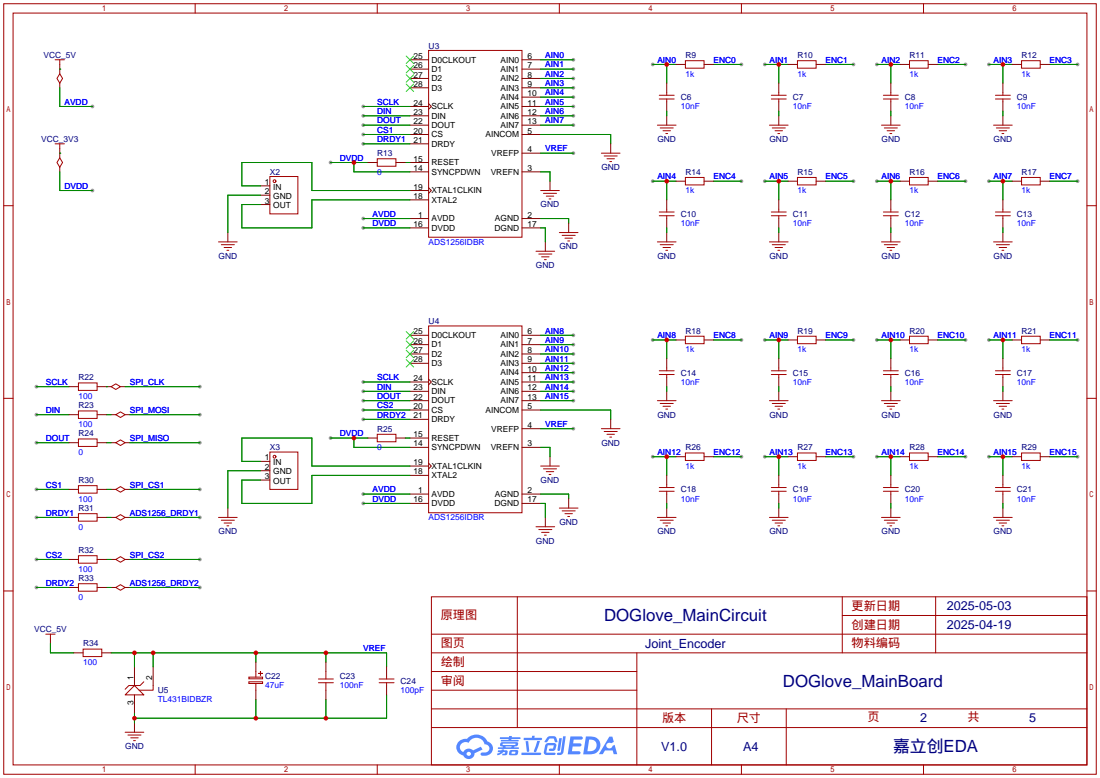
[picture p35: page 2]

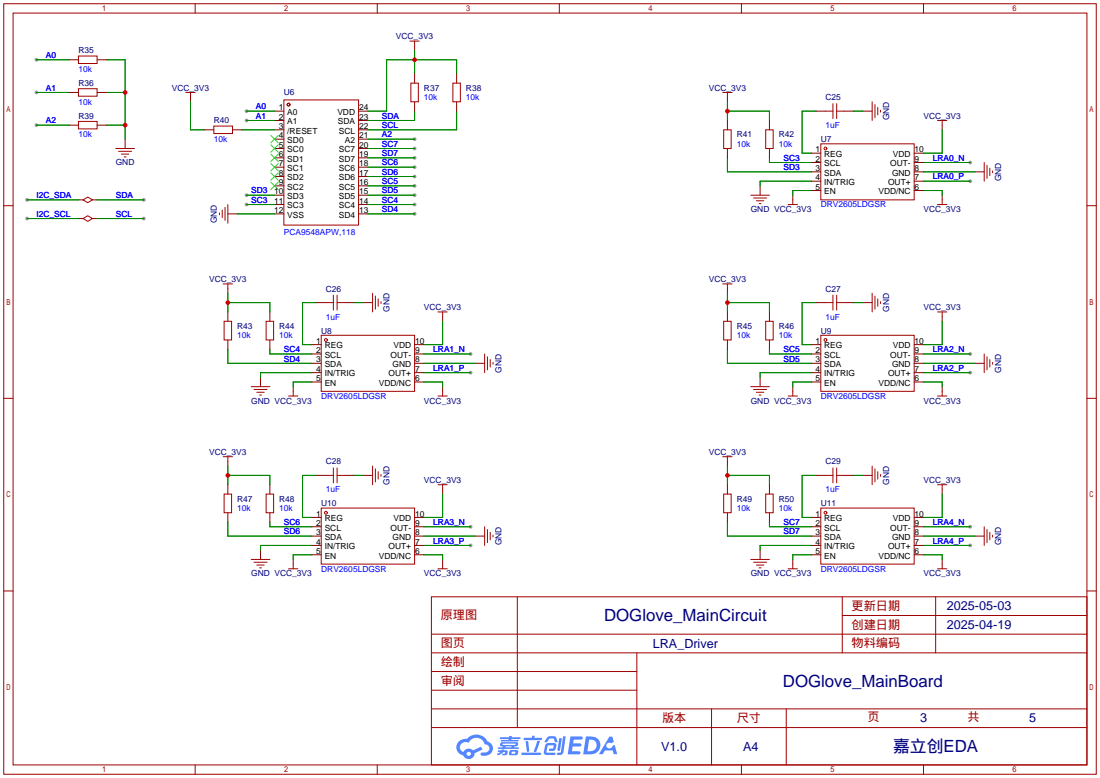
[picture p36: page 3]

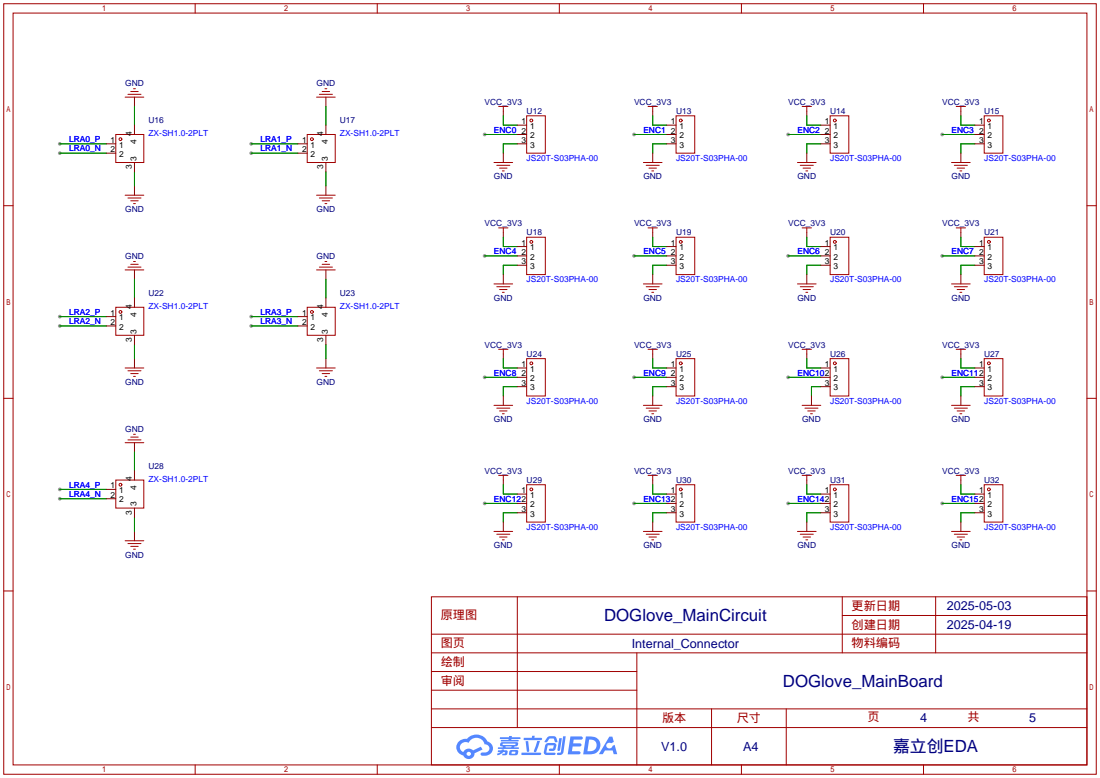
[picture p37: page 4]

U2D2

# UART

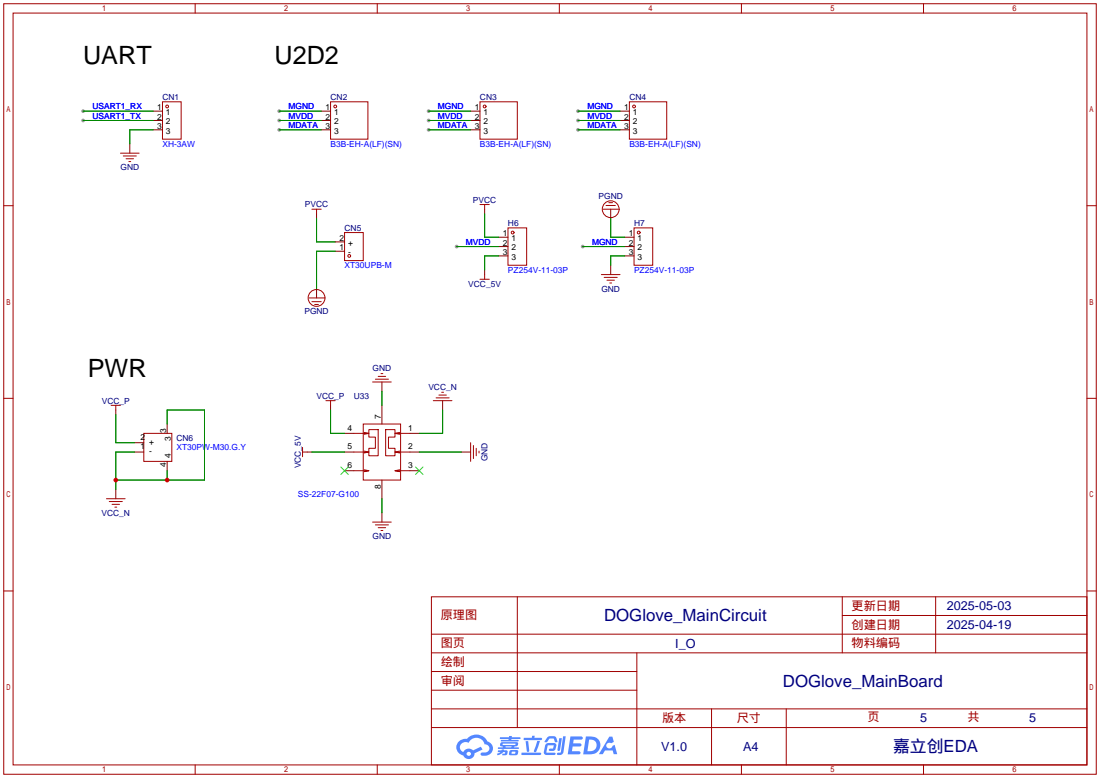
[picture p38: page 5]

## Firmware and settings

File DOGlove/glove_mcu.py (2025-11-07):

import socket
import struct
import threading
import time

import serial

import numpy as np

# Configure your UART port and baud rate
uart_port = "/dev/ttyACM0"  # Main board UART port
# uart_port = "/dev/tty.usbmodem57340031741"  # Main board UART port
baud_rate = 921600  # Main board baud rate

# Define the header you are looking for
header = bytes([0xAA, 0x55, 0x00, 0x00])
data_length = 16  # Number of data values in the block
block_size = 76  # Total size including header, data, and CRC

# Configure UDP settings
udp_ip = "127.0.0.1"  # Localhost IP
udp_port = 5009  # Port for joint data
udp_port_servo = 5010  # Port for servo data
# udp_port_lra = 5012  # Port for LRA data

class UARTReader:
    def __init__(self):
        self.buffer = bytearray()
        self.running = True
        self.serial_port = serial.Serial(uart_port, baud_rate, timeout=1)
        self.udp_socket = socket.socket(socket.AF_INET, socket.SOCK_DGRAM)
        # self.sock = socket.socket(socket.AF_INET, socket.SOCK_DGRAM)
        # self.sock.bind((udp_ip, udp_port_lra))
        self.write_fps = 30

    def read_from_uart(self):
        while self.running:
            # print("Reading from UART...")
            data = self.serial_port.read(self.serial_port.in_waiting or 1)
            if data:
                self.buffer.extend(data)
                self.process_buffer()
            else:
                print("No data received from UART")

    def process_buffer(self):
        while len(self.buffer) >= block_size: # Check if the buffer has enough data to process
            # Find the start index of the first header
            start_index = self.buffer.find(header)

            # No header found, clear the buffer if it's longer than the block size
            if start_index == -1:
                print("No header found. Check the alignment of the data.")

                # If no header is found, clear the buffer if it's longer than the block size
                if len(self.buffer) > block_size:
                    print(f"Discarded data: {self.buffer[:block_size].hex()}")
                    self.buffer = self.buffer[-block_size:]
                break

            # Header found at the beginning of the buffer
            elif start_index == 0:
                # Now find the next header
                next_header_index = self.buffer.find(header, len(header))
                if next_header_index == -1:
                    # If no header is found, break and wait for more data
                    # print(f"No complete block found. Waiting for more data...")#: {self.buffer.hex()}")
                    break
                elif (next_header_index - start_index) != block_size:
                    # If the block is corrupted, discard the data
                    print(f"Corrupted block found: {self.buffer[:next_header_index].hex()}")
                    self.buffer = self.buffer[next_header_index:]
                else:
                    # We found a complete block
                    block = self.buffer[start_index:next_header_index]
                    self.process_block(block)

                    # Remove the processed block from the buffer
                    self.buffer = self.buffer[next_header_index:]
            
            # Header found in the middle of the buffer, discard the data before the header
            else:
                print(f"Discarded data: {self.buffer[:start_index].hex()}")
                self.buffer = self.buffer[start_index:]

    def process_block(self, block):
        # Unpack the block (skip the header)
        data = struct.unpack("<I16iI", block[4:]) # uint32_t reference, 16 int32_t values, uint32_t CRC

        # Extract the 16 int32_t values and CRC
        reference_voltage = data[0]
        data_values = data[1:-1]
        crc = data[-1]

        # Convert data_values to voltages
        voltages = [(float(val) * 5.0 / 0x7FFFFF) for val in data_values]

        # Split CRC into checksum and timestamp
        checksum = (crc >> 16) & 0xFFFF
        timestamp = crc & 0xFFFF

        # Calculate the expected checksum (16-bit sum of data_values)
        expected_checksum = sum(data[:-1]) & 0xFFFF

        # Calculate the joint angles
        reference_voltage = reference_voltage/1000000 # Convert to volts
        joint_angles = [val/reference_voltage*360 for val in voltages if reference_voltage != 0]

        print(f"Voltages: {[round(val, 2) for val in voltages]}")
        print(f"Joint Angle: {[round(val, 2) for val in joint_angles]}")
        print(f"Timestamp: {int(timestamp)}")
        print(f"Checksum: {(checksum)} (Expected: {(expected_checksum)})")
        print(f"Checksum Valid: {checksum == expected_checksum}")
        print("-" * 40)

        # Send the first voltage value via UDP
        # message = struct.pack("f", voltages[0])
        format_string = "f" * len(joint_angles)
        # Pack all the values in the list
        message = struct.pack(format_string, *joint_angles)
        self.udp_socket.sendto(message, (udp_ip, udp_port))
    
    # def lra_control(self, channel, wave, duration):
    #     """send_data = 0x55, 0xAA, channel(0-4), wave, duration_h, duration_l, checksum"""
    #     if channel not in range(5):
    #         print("Invalid channel. Please choose a channel between 0-4.")
    #         return
    #     if wave not in range(256):
    #         print("Invalid wave. Please choose a wave between 0-255.")
    #         return
    #     if duration not in range(65536):
    #         print("Invalid duration. Please choose a duration between 0-65535.")
    #         return
    #     duration_H = (duration >> 8) & 0xFF
    #     duration_L = duration & 0xFF
    #     checksum = (channel + wave + duration_H + duration_L) & 0xFF
    #     send_data = [0x55, 0xAA, channel, wave, duration_H, duration_L, checksum]
    #     # print(f"send data: {bytes(send_data).hex()}")
    #     self.serial_port.write(bytes(send_data))
    
    # def listen(self):
    #     print(f"Listening on {udp_ip}:{udp_port_lra}...")
    #     while self.running:
    #         data, addr = self.sock.recvfrom(4*4)  # 4 bytes per float, 16 floats
    #         if data:
    #             # Unpack the received float
    #             received_kp = struct.unpack("f"*4, data)

    #             # Store the most recent pressure
    #             self.most_recent_kp = received_kp

    #             # print(f"Received kp (as float): {kp}")
    #             # print("-" * 40)

    #             # Control the LRA
    #             k = 100
    #             # k = 2000
    #             for i in range(len(received_kp)):
    #                 if received_kp[i] > 10 and received_kp[i] < k:
    #                     self.lra_control(i, 56, int(1000/self.write_fps))
    #                     # self.lra_control(i, 222, int(1000/self.write_fps))
    #                 else:
    #                     self.lra_control(i, 222, 100)
    #             time.sleep(1/self.write_fps)

    def start(self):
        print("UART reader started")
        self.thread = threading.Thread(target=self.read_from_uart)
        self.thread.start()
        # self.thread_lra = threading.Thread(target=self.listen)
        # self.thread_lra.start()

    def stop(self):
        print("Closing UART port...")
        self.running = False
        self.thread.join()
        # self.thread_lra.join()
        self.udp_socket.close()
        # self.sock.close()
        self.serial_port.close()
        

class UDPReceiver:
    def __init__(self):
        self.most_recent_joints = None
        self.most_recent_servo = None
        self.urdf_joints = None
        self.running = True
        self.sock1 = socket.socket(socket.AF_INET, socket.SOCK_DGRAM)
        self.sock1.bind((udp_ip, udp_port))
        self.sock2 = socket.socket(socket.AF_INET, socket.SOCK_DGRAM)
        self.sock2.bind((udp_ip, udp_port_servo))
        self.length = data_length

    def listen1(self):
        print(f"Listening on {udp_ip}:{udp_port}...")
        while self.running:
            data, addr = self.sock1.recvfrom(4*self.length)  # 4 bytes per float, 16 floats
            if data:
                # Unpack the received float
                received_joints = struct.unpack("f"*self.length, data)

                # Store the most recent joint angle
                if received_joints is not None:
                    self.most_recent_joints = received_joints

                    # print(f"Received joint angle (as float): {received_joints}")
                    # print(f"Converted joint angle (as int): {self.most_recent_joints}")
                    # print("-" * 40)
            
    def listen2(self):
        print(f"Listening on {udp_ip}:{udp_port_servo}...")
        while self.running:     
            data, addr = self.sock2.recvfrom(4*5)  # 4 bytes per float, 5 floats
            if data:
                # Unpack the received float
                received_servo = struct.unpack("f"*5, data)

                # Store the most recent servo angle
                if received_servo is not None:
                    self.most_recent_servo = received_servo

                    # print(f"Received servo angle (as float): {received_servo}")
                    # print(f"Converted servo angle (as int): {self.most_recent_servo}")
                    # print("-" * 40)

    def start(self):
        self.thread1 = threading.Thread(target=self.listen1)
        self.thread1.start()

        self.thread2 = threading.Thread(target=self.listen2)
        self.thread2.start()

    def stop(self):
        self.running = False
        self.thread1.join()
        self.thread2.join()
        
        self.sock1.close()
        self.sock2.close()

    def convert_to_urdf_joint(self):
        # Convert the joint angle to URDF joint angle
        joint_angles = self.most_recent_joints
        servo_angles = self.most_recent_servo

        if joint_angles is not None and servo_angles is not None:
            urdf_joint_angles = [0.0] * 21

            urdf_joint_angles[0] = np.deg2rad(-(joint_angles[0]-90)) # 0 - thumb_dip
            urdf_joint_angles[1] = np.deg2rad(joint_angles[1]-270) # 1 - thumb_pip
            urdf_joint_angles[2] = np.deg2rad(joint_angles[2]-180) # 2 - thumb_mcp_s
            urdf_joint_angles[3] = np.deg2rad(joint_angles[3]-270) # 3 - thumb_mcp_r

            urdf_joint_angles[4] = np.deg2rad(-(joint_angles[4]-90)) # 4 - index_dip
            urdf_joint_angles[5] = np.deg2rad(joint_angles[5]-270) # 5 - index_pip
            urdf_joint_angles[6] = np.deg2rad(-(joint_angles[6]-180)) # 6 - index_mcp_s

            urdf_joint_angles[7] = np.deg2rad(-(joint_angles[7]-90)) # 7 - middle_dip
            urdf_joint_angles[8] = np.deg2rad(joint_angles[8]-270) # 8 - middle_pip
            urdf_joint_angles[9] = np.deg2rad(-(joint_angles[9]-180)) # 9 - middle_mcp_s

            urdf_joint_angles[10] = np.deg2rad(-(joint_angles[10]-90)) # 10 - ring_dip
            urdf_joint_angles[11] = np.deg2rad(joint_angles[11]-270) # 11 - ring_pip
            urdf_joint_angles[12] = np.deg2rad(-(joint_angles[12]-180)) # 12 - ring_mcp_s

            urdf_joint_angles[13] = np.deg2rad(-(joint_angles[13]-90)) # 13 - little_dip
            urdf_joint_angles[14] = np.deg2rad(joint_angles[14]-270) # 14 - little_pip
            urdf_joint_angles[15] = np.deg2rad(-(joint_angles[15]-180)) # 15 - little_mcp_s

            urdf_joint_angles[16] = np.deg2rad(-(servo_angles[0]-182.2)) # 16 - thumb_mcp_b
            urdf_joint_angles[17] = np.deg2rad(-(servo_angles[1]-165.2)) # 17 - index_mcp_b
            urdf_joint_angles[18] = np.deg2rad(-(servo_angles[2]-150.29)) # 18 - middle_mcp_b
            urdf_joint_angles[19] = np.deg2rad(-(servo_angles[3]-151.44)) # 19 - ring_mcp_b
            urdf_joint_angles[20] = np.deg2rad(-(servo_angles[4]-145.9)) # 20 - little_mcp_b

            urdf_joint_angles = tuple(urdf_joint_angles)

            self.urdf_joints = urdf_joint_angles


    def get_most_recent_joints(self):
        self.convert_to_urdf_joint()
        #print(self.urdf_joints)
        return self.urdf_joints


if __name__ == "__main__":
    reader = UARTReader()
    try:
        print(f"Opening UART port {uart_port} at {baud_rate} baudrate...")
        reader.start()
        print("UART port opened successfully")

        # Keep the main thread alive
        while True:
            time.sleep(1)

    except KeyboardInterrupt:
        print("Program interrupted by user")

    finally:
        reader.stop()

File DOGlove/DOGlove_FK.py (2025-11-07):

from pathlib import Path
import mujoco
import mujoco.viewer
# import numpy as np
from loop_rate_limiters import RateLimiter

# import mink

from glove_mcu import UDPReceiver

_HERE = Path(__file__).parent
_XML = _HERE / "DOGlove_meshes" / "DOGlove-v3.xml"




def get_body_pos(model, data, body_name):
    body_id = mujoco.mj_name2id(model, mujoco.mjtObj.mjOBJ_BODY, body_name)
    body_pos = data.xpos[body_id]
    return body_pos

def get_site_pos(model, data, site_name):
    site_id = mujoco.mj_name2id(model, mujoco.mjtObj.mjOBJ_SITE, site_name)
    site_pos = data.site_xpos[site_id]
    return site_pos

def find_actuator_for_joint(model, joint_name):
    """Finds the actuator controlling the given joint."""
    joint_id = mujoco.mj_name2id(model, mujoco.mjtObj.mjOBJ_JOINT, joint_name)
    
    # Iterate through actuators to find the one controlling this joint
    for actuator_id in range(model.nu):  # `nu` is the number of actuators
        # `actuator_trnid` gives the joint or tendon that each actuator controls
        # actuator_trnid[actuator_id, 0] contains the joint/tendon ID
        if model.actuator_trnid[actuator_id][0] == joint_id:
            return actuator_id
    return None


def main():
    model = mujoco.MjModel.from_xml_path(_XML.as_posix())
    data = mujoco.MjData(model)

    receiver = UDPReceiver()
    receiver.start()

    try:
        with mujoco.viewer.launch_passive(
            model=model, data=data) as viewer:
            mujoco.mjv_defaultFreeCamera(model, viewer.cam)
            mujoco.mj_forward(model, data)
            
            rate = RateLimiter(frequency=100.0)
            
            site_names = ['index_tip_site', 'middle_tip_site', 'ring_tip_site', 'little_tip_site', 'thumb_tip_site']
            
            joint_names = ['thumb_bend_1', 'thumb_bend_2', 'thumb_split', 'thumb_mcp', 
                           'index_bend_1', 'index_bend_2', 'index_split', 
                           'middle_bend_1', 'middle_bend_2', 'middle_split', 
                           'ring_bend_1', 'ring_bend_2', 'ring_split', 
                           'pinky_bend_1', 'pinky_bend_2', 'pinky_split',
                           'thumb_bend_3', 'index_bend_3', 'middle_bend_3', 'ring_bend_3', 'pinky_bend_3']
            # Initialize lists to store joint IDs and qpos indices
            joint_ids = []
            qpos_indices = []

            for joint_name in joint_names:
                joint_id = mujoco.mj_name2id(model, mujoco.mjtObj.mjOBJ_JOINT, joint_name) # Get joint ID for each joint name
                qpos_index = model.jnt_qposadr[joint_id] # Get the corresponding qpos index
                # print(f"Joint Name: {joint_name}, Joint ID: {joint_id}, Qpos index: {qpos_index}")
                
                # Append joint_id and qpos_index to their respective lists
                joint_ids.append(joint_id)
                qpos_indices.append(qpos_index)

            # # Initialize the control value
            # ctrl_value = 0.1
            # increment = 0.1

            while viewer.is_running():
                mujoco.mj_step(model, data)
                
                for name in site_names:
                    site_pos = get_site_pos(model, data, name)
                    # print(f"{name}: {site_pos}")
                
                # print(f"Qpos: {data.qpos}")
                # data.qpos[qpos_index] = 0.5 # Set the joint angle
                # data.ctrl[joint_id] = 0.5 # Set the control value (this should drive the joint)
                # mujoco.mj_forward(model, data)
                # print(f"Index_dip joint angle: {data.qpos[qpos_index]}")

                # # Set the control value gradually, from 0.1 to 0.7
                # data.ctrl[joint_id] = ctrl_value
                # mujoco.mj_forward(model, data)

                # # Increment control value
                # ctrl_value += increment
                # if ctrl_value > 2.6:
                #     ctrl_value = 0.1  # Reset to start the cycle again

                # Get the most recent joint angles from the glove
                joints = receiver.get_most_recent_joints()
                if joints is not None:
                    # print(f"Index DIP: {round(joints[4], 2)}")
                    for i in range(len(joints)):
                        print(f"Joint[{i}]= {round(joints[i], 2)}")
                        data.ctrl[joint_ids[i]] = joints[i]
                    mujoco.mj_forward(model, data)
                
                # Visualize at fixed FPS.
                viewer.sync()
                rate.sleep()

    except KeyboardInterrupt:
        print("Program interrupted by user")

    except KeyboardInterrupt:
        print("Program interrupted by user")

    finally:
        receiver.stop()
        print("UDP receiver stopped successfully")

if __name__ == '__main__':
    main()

    finally:
        receiver.stop()
        print("UDP receiver stopped successfully")

if __name__ == '__main__':
    main()
